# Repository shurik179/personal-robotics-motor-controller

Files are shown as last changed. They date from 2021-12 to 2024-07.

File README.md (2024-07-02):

# Personal Robotics Motor Controller

This repository contain design files for a 2-channel motor
controller board, designed by members of Personal Robotics discord server.

The controller is based on [DRV8874](https://www.ti.com/lit/ds/symlink/drv8874.pdf) motor driver ICs by TI. The  key
features of this controller are listed below:

* Support for 2 brushed DC motors, 5-24v

* Current limit per channel: 4.5A continuous (with heatsinks), current limited

* Overcurrent, undervoltage, and overtemperature protection

* Support for quadrature encoders for each motor (3.3v)

* An on-board MCU (RP2040) for reading encoder input and
  providing variety of close loop motor control modes

* Serial interface for control by a microcontroller or single board computer

This repository contains both board design files (as KiCad 6.0 project) and
firmware (written using Arduino IDE with Earl Philhower arduino-pico core for RP2040).

Detailed project information is available http://motor-controller.rtfd.io/

## Copyright

This project was started in 2021  by:

* Ichiro Furusato  (https://github.com/ifurusato)

* Adam Green (https://github.com/adamgreen/)

* shurik179 (https://github.com/shurik179)

It is released under Apache license; see file LICENSE for details.

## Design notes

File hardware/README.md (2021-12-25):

# Hardware

This directory contains:

* Board design files (in KiCad 6.0 format)

* Bill of Materials (BOM)

The board specs are:

* Dimensions: 60x50 mm

* Stackup: 4-layer, 1.6mm thickness, 1oz copper thickness (outzide layers)

* Mounting holes: 4 holes for M3 screws, in the shape of rectangle 43x53mm

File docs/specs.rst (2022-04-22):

.. _specs:
**************************
Specifications
**************************

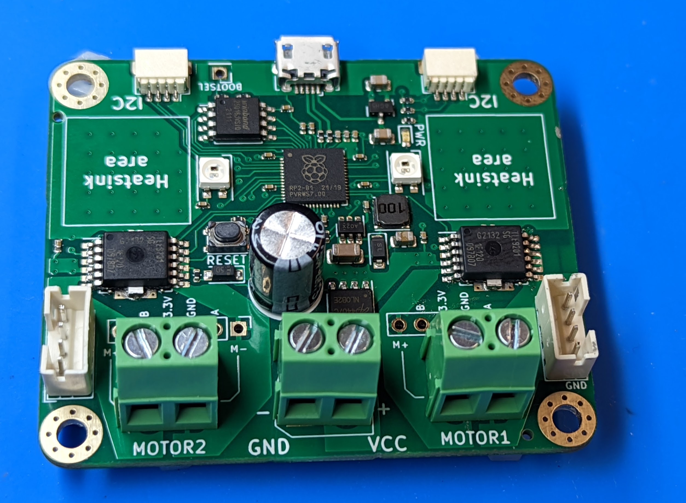
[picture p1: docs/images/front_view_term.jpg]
Top view


Overview
=========
The Personal Robotics  Motor Controller (which from now on will be abbreviated to PRMC)
can be used to control two brushed DC motors (5-18V) with quadrature encoders.
It provides position and speed reading (if encoders are present) and closed-loop
mode in which it keeps motor speed constant using encoder feedback and PID algorithm.

I2C interface
=============
PRMC is controlled by a host MCU (Arduino or similar boards) or
single board computer such as Raspberry Pi using I2C interface.
It uses 3.3v I2C bus, at up to 400 kHz speed. There are two identical
Qwiic/Stemma QT connectors allowing one to daisy-chain several controllers.

PRMC includes 10k pullups to 3.3v  on SCL and SDA lines; you might want to add
additional pullups on the i2c master.

**Important**: the 3.3v pin of the Qwiic connectors is unconnected. Instead,
PRMC uses its own voltage regulator to provide power to the built-in electronics.
This also means that when daisy-chaining, it will not provide power to other I2C devices.

By default, the controller uses I2C address `0x54` (or 84 in decimal form).
It can be changed by closing solder bridge jumpers on the bottom side  of the
board, below label `I2C ADDR`:

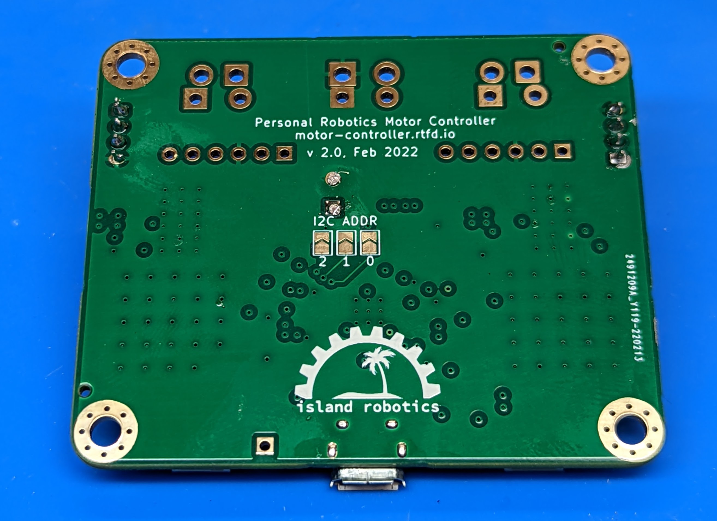
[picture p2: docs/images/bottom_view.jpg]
Bottom view


* closing jumper labeled `0` sets bit 0, adding  1 to the address

* closing jumper labeled `1` adds 2 to the address

* closing jumper labeled `2` adds 4 to the address

Thus, by using different combinations of the jumpers, one can get any address between
`0x54` (decimal 84) and `0x5A` (decimal 91), allowing one to use up to 8 such
motor controllers on the same bus.

Power supply
============
PRMC is intended for use with  motor power supply of **5--18V**. Absolute maximum
voltage for power supply is 24V; voltages above that will damage PRMC. Please
note that actual voltage provided by the battery can be higher than nominal voltage:
e.g., a 10-cell NiMH battery pack has nominal voltage of 12V but in fact a fully
charged pack can read as high as 14V.

The power supply connection has
reverse polarity protection preventing damage if the power leads are switched.
It also has limited  ESD protection to protect  it from spikes caused by electrostatic discharge.

PRMC contains a voltage regulator (a combination of buck converter and an LDO) providing
3.3v power to on-board electronics from the motor power supply.

Electronics
===========
Key components of PRMC are two `TLE9201SG <https://www.infineon.com/cms/en/product/power/motor-control-ics/brushed-dc-motor-driver-ics/integrated-full-bridge-driver/tle9201sg/>`__ motor controller
ICs by Infineon; please read the IC  datasheet for details of their operation.

PRMC also contains an RP2040 MCU by Raspberry Pi. It is preloaded with firmware
providing I2C interface, reading quadrature encoders, and providing closed loop motor control.

Indicator LEDs
==============
PRMC includes a green power indicator LED; it lights up whenever the board is powered.
In addition, it has two NeoPixel LEDs used to show the status of motors as follows:

 - Blue: firmware running, but no I2C connection yet

 - Green: motor enabled

 - Red: motor disabled (either by command from  host MCU or because of triggered
   protection such as overtemperature protection).

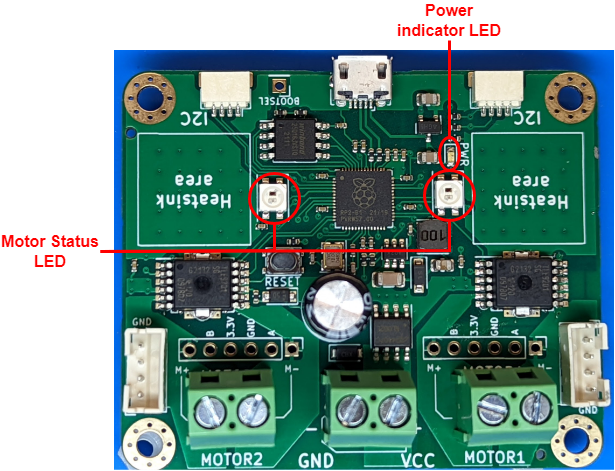
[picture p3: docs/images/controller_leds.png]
LEDs


Connections
===========

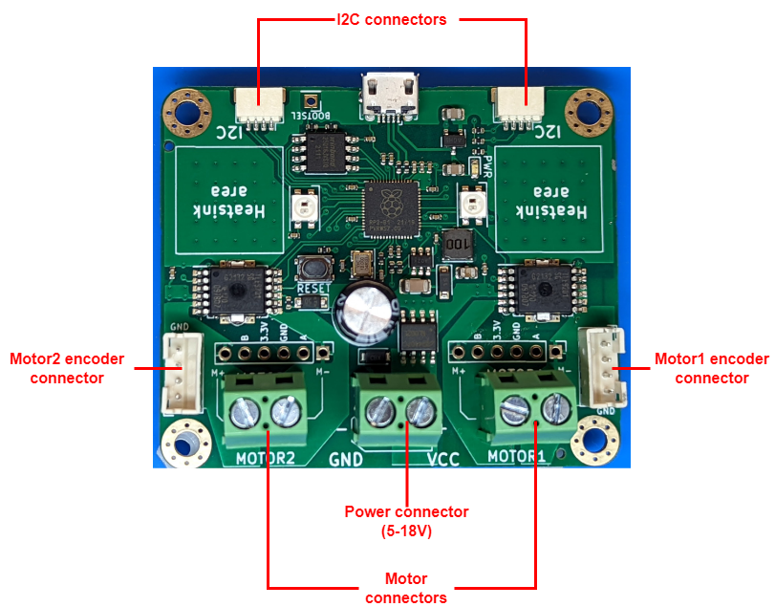
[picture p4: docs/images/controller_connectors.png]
connections


The board provides several options for connecting motors, encoders, and main power:

* Motor connections: you can choose between

  - 5mm pitch **screw terminal** (we use high-quality rising cage type terminals)

  - **JST VH** connector (same as used by First Tech Challenge robotics competitions)

  - 6pin **male headers** (matching pinout of `22mm motors <https://www.servocity.com/142-rpm-premium-planetary-gear-motor-w-encoder/>`__
    sold by Servocity). These connectors provide both motor power and encoder connectors.
    Note: 6pin  connectors used by other motors - e.g.
    `25mm motors <https://www.pololu.com/product/4865>`__ from Pololu - may use different pin order.

* Encoder connections: a 4-pin JST PH connector, using the following pin order:

  - Pin 1: GND;

  - Pin 2: 3.3V;

  - Pin 3: Channel A;

  - Pin 4: Channel B.

  (This matches the pin order of
  `REV control hub <https://www.revrobotics.com/rev-31-1595/>`__ used in First Tech Challenge robotics competitions.)

* Main power: 5mm pitch **screw terminal** or **XT30** male connector

* I2C connectors: the board provides two Qwiic/Stemma QT I2C connectors.
  This makes it possible to daisy-chain connectors. (Note: I2C connector doesn't
  provide 3.3v power, see above.)

The photos below show PRMC with different combinations of connectors.

* With  **screw terminals** for main power and motors:

   Top view

* With  **screw terminals** for main power and **male headers** for motor
  connectors

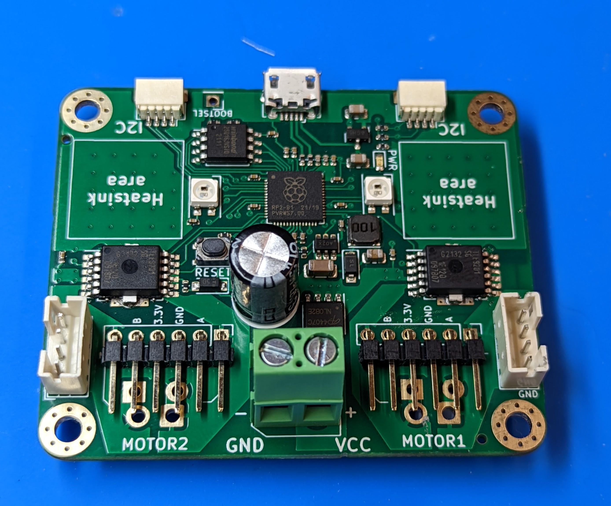
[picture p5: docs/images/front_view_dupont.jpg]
Top view
   

* With **XT30** male connector  for main power and **JST VH2** connectors for motors:

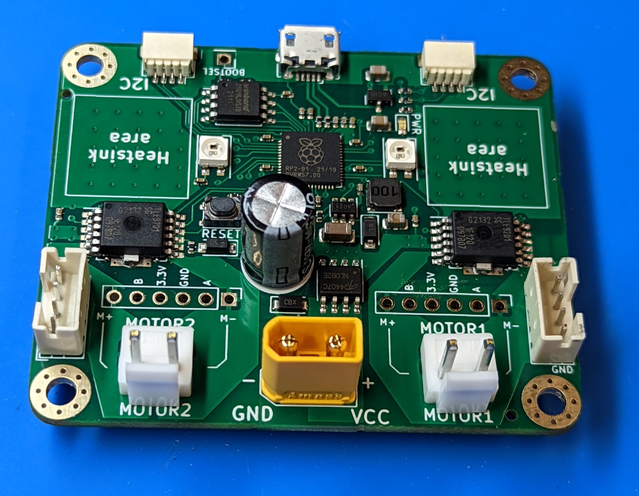
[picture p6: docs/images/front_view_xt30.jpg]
Top view
   

Current limit
=============
Motor driver ICs provide current limiting: if the output current exceeds 8A,
the drivers will start "chopping" the current, preventing it from ever exceeding 8A.
This makes it possible  to use the controller with motors with stall current over 8A.

However, 8A can only be sustained for short period of time; at this current,
the board will overheat quickly. Our testing shows that the board can continuously
provide 3.5A per channel in default configuration.

The board also contains two areas to which one can attach optional 14mm square heatsinks
(which are commonly used for Raspberry Pi single board computers and thus are
easily available from many vendors). With the heatsinks attached, the board can
provide up to 4.5A  continuous per channel.

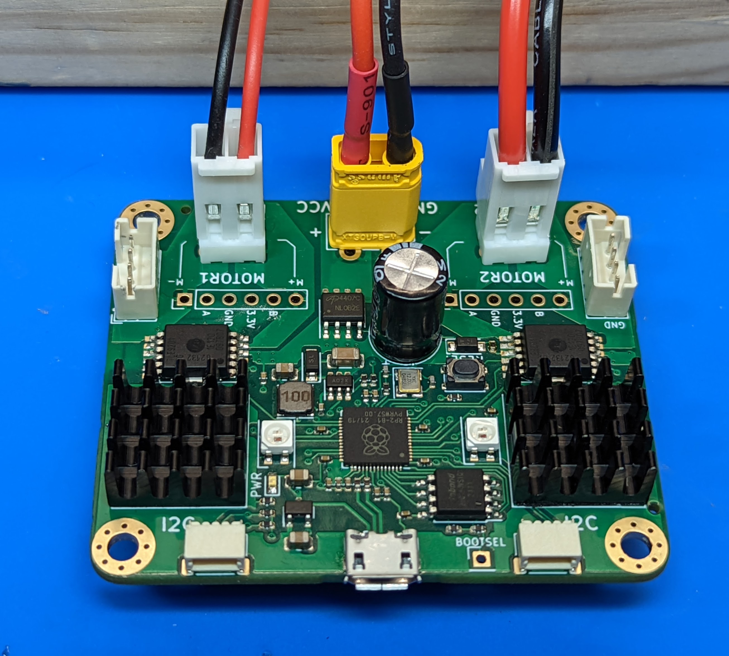
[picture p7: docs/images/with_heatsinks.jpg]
With heatsinks


Protection features
===================
In addition to current limiting listed above, the motor drivers also provide
variety of other protection features:

* undervoltage

* overtemperature

* short circuit

Please see the TLE9201 `datasheet <https://www.infineon.com/dgdl/Infineon-TLE9201SG-DS-v01_00-en.pdf?fileId=db3a304345087709014518190f481cec>`__ for details.

If any of the protection features are triggered, the IC automatically disables
motor output. Firmware allows the user to check the motor status to see if
the output has been disabled and if desired, re-enable it.

Dimensions
===========
The board dimensions are 50x60mm. Board height depends on the chosen connectors;
with screw terminals, height is about 14mm. If you use JST VH for motors or XT30
connector for power, you will need at least 22mm clearance above the PCB for the
connector and cables.

There are four mounting holes for M3 or smaller screws; their position is
shown in the diagram below.

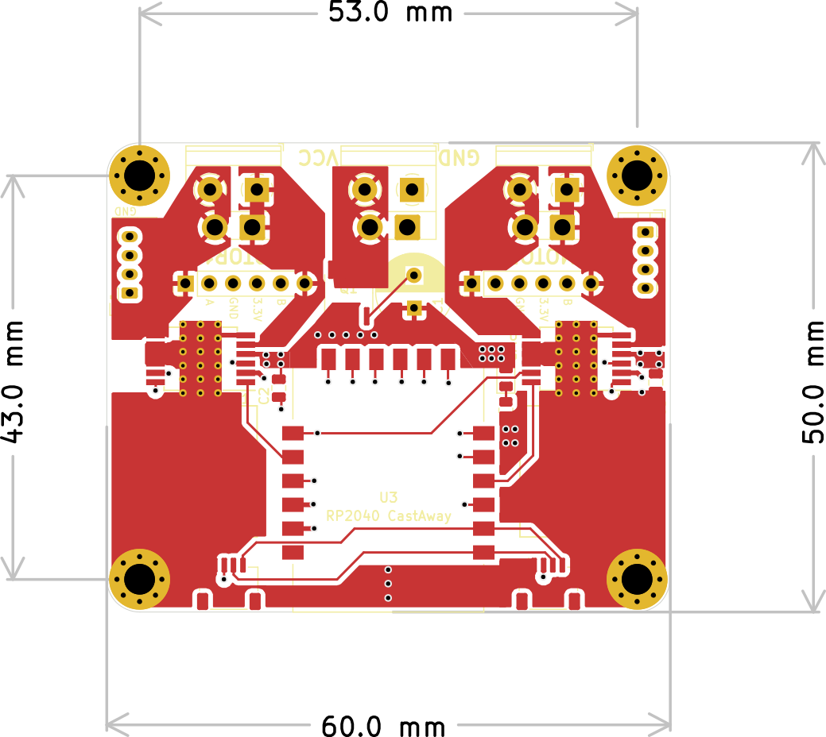
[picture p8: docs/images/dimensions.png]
Board dimensions


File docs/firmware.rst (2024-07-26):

.. _firmware:
**************************
Firmware and register map
**************************

Firmware
========

The firmware for the PRMC motor controller  is written in Arduino IDE using
Earl Philhower's `RP2040 core <https://github.com/earlephilhower/arduino-pico>`__.

If you want to modify it, you can find source files in `firmware` folder in |github|. 
Make sure to select `Boot Stage 2: W25Q16JVxQ QSPI/4` option in `Tools` menu. 

I2C communication
=================

PRMC is controlled via UART 
FIXME 
All multibyte registers use little-endian encoding; e.g. for register
`REG_POWER1`, low byte is at address 12, and high byte, at address 13.

.. csv-table:: Register map
   :widths: 10 10 30 10 50
   :header:   "register(s)","R/W","Name","data type","description"

   0,R/W,REG_ENABLE,byte,"Enable/disable motors. Bit0 controls motor1 (1=enable, 0=disable); bit1 controls motor2"
   1,R/W,REG_PID_MODE,byte,"0: normal control, PID off; 1: PID on (individual motors)"
   2-3,R/W,REG_MAX_SPEED,uint16,Max motor speed in encoder ticks/s. Required for PID
   4-5,R/W,REG_PID_KP,uint16,Kp*10^7
   6-7,R/W,REG_PID_TI,uint16,Ti*1000
   8-9,R/W,REG_PID_TD,uint16,Td*1000
   10-11,R/W,REG_PID_ILIM,uint16,Ilim
   12-13,R/W,REG_POWER1,int16,"Motor1 power, -1000...1000. Used both in PID on and PID off modes, see details in "
   14-15,R/W,REG_POWER2,int16,"Motor2 power, -1000...1000"
   16,R/W,REG_REVERSE,byte,Bit0: should readings of encoder 0 be reversed? Bit2: same for encoder2
   24,R,REG_FW_VERSION,uint8,Firmware version - minor
   25,R,,uint8,Firmware version - major
   26,R,REG_WHO_AM_I,uint8,0x54 (used for testing connection)
   27,R,REG_STATUS,uint8,"Status. Bit0 is motor1, bit1 is motor2. If motor is disabled, corresponding bit is set; otherwise, bit=0"
   28-31,R,REG_ENCODER1,int32,"Encoder 1 value, ticks"
   32-35,R,REG_ENCODER2,int32,"Encoder 2 value, ticks"
   36-37,R,REG_SPEED1,int16,"Motor 1 speed, in ticks/s"
   38-39,R,REG_SPEED2,int16,"Motor 2 speed, in ticks/s"

Motor control: basic
====================

By default, PRMC has both motor drivers enabled, with PID mode off. To set the
motor power just write a value between -1000 and 1000 to register `REG_POWER1`
for motor 1 (respectively, `REG_POWER2` for motor 2).

To disable one or both motor drivers, write the corresponding value to `REG_ENABLE`.
Note that the motor driver can also be disabled because one of the driver IC
protection features, such as overtemperature protection, were triggered.
You can check if a motor is enabled or disabled by reading `REG_STATUS`.
If necessary, you can re-enable a motor by writing to `REG_ENABLE`.

Encoders
========
PRMC supports quadrature encoders for each motor, recording encoder values
and speeds to registers `REG_ENCODERx` and `REG_SPEEDx`. It counts both
rising and falling edge for each of quadrature encoder channels, thus producing
4 ticks per encoder cycle. Both encoder values and speeds can be positive or
negative depending on the rotation direction.

Note that encoder value is recorded as 32-bit integer, so it will overflow at
2,147,483,648 ticks. Similarly, encoder speed is 16-bit integer, so it will
overflow at 32,768 ticks/s. This should be more than enough for common hobby
motors; e.g. a popular
`GoBilda Yellow Jacket <https://www.gobilda.com/5202-series-yellow-jacket-planetary-gear-motor-26-9-1-ratio-223-rpm-3-3-5v-encoder/>`__
motor has  no-load  speed of about 3000 encoder ticks/s.

For normal operation of PID control (see next section), it is expected that
providing positive power to the motor gives positive speed as measured by the encoder.
If your motor and encoder are wired so that positive power to motor gives negative
encoder counts, you can either change the wiring, or change the encoder direction
in software by writing to `REG_REVERSE`.

PID control
===========

Motor driver firmware provides an option of closed loop motor control. In this mode,
the controller tries to keep the speed of each motor (as measured using encoders)
as close as possible to the desired speed, using industry-standard PID
(proportional-integral-derivative) algorithm.

The motor power is determined by the standard formula of PID algorithm:

.. math::
   M=M_0+ P + I_{clipped} + D

where:

:math:`M` is motor power (ranging from -1.0 to 1.0)

:math:`M_0=v_{target}/v_{max}` is the zero-level approximation; here
:math:`v_{target}` is the requested speed (in ticks/s) and :math:`v_{max}` is the maximal
possible motor speed, which is determined by motor's no-load RPM

:math:`P=K_p e` is the proportional term. Here
:math:`e=v_{target}-v_{actual}` is the error, i.e. the  difference of desired and actual motor
speeds (measured in encoder ticks/sec) and :math:`K_p` is a coefficient

:math:`I=\frac{K_p}{T_i}\int e dt` is the integral term; :math:`I_{clipped}` is
:math:`I` but clipped to be between :math:`-I_{lim}` and :math:`I_{lim}`

:math:`D=K_p T_d \frac{d}{dt} e` is the  derivative
of the error

:math:`K_p, T_i, T_d, I_{lim}` are the PID coefficients. They **must  be set
(by writing to corresponding registers) before PID mode can be used**; there
are no default values.

The behavior of the PID algorithm is determined by these coefficients; for
example, if the coefficient :math:`K_p` is too small, it will take the motor a
long time to stabilize to the desired speed; if the coefficient :math:`K_p` is
too large, you might get oscillations. Choosing the correct coefficients
requires significant experience and is certainly outside the scope of this user
guide.

Please note that current version of firmware uses same PID coefficients for
both motors; setting them independently for the two motors is not supported.

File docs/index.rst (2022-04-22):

##################################
Personal Robotics Motor Controller
##################################
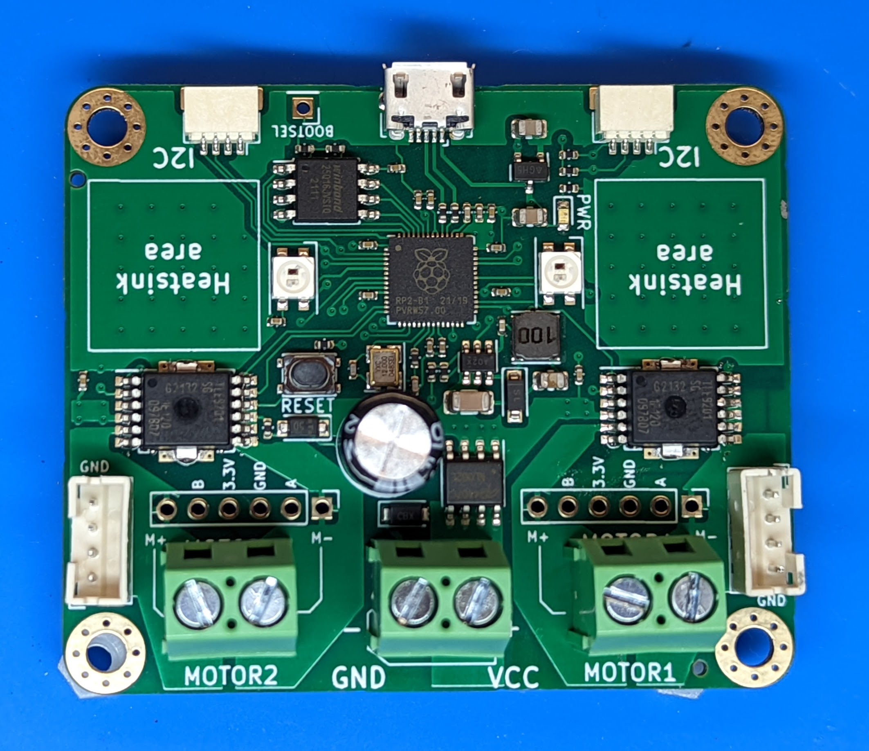
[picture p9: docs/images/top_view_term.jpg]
Motor driver


This guide contains documentation for a dual channel controller for DC motors.
This controller was created by group of robotics enthusiasts from Personal Robotics
discord server, who needed a mid-power dual channel motor controller supporting
closed loop motor control but were not ready to pay $70 and more for existing
commercial realizations. So we created our own - and made it available on Tindie:
https://www.tindie.com/products/26573/

Key features of this controller are as follows:

* support for **2 brushed DC motors**

* Motor voltage: **5-18v**; reverse polarity protection for power input

* Current per channel

  - **8A peak**, current limited

  - **3.5A continuous** if used without heatsinks

  - **4.5A continuous** with optional heatsinks

* Support for **quadrature encoders**  for each channel. Note: it uses
  **3.3v for encoders** - make sure your encoders support that (many encoders
  require 3.5V or above)

* **Closed loop speed control**, using PID algorithm

* Variety of **protection features**: automatic overcurrent, overtemperature,
  undervoltage, and short circuit protection

* Controlled by a host microcontroller  or single board computer such as Raspberry Pi
  using **I2C interface**. MicroPython library is available

All design files and software are available from the project |github| under open
source license.

This document describes version 2.0 of the project, released in April 2022.

.. toctree::
    :caption: Table of Contents
    :maxdepth: 1

    specs
    firmware
    mp_library
    license

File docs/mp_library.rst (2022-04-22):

.. _library:
**************************
Micropython Library
**************************
This chapter documents included Micropython library.

Installation
============
To install the library, download the latest version of `PRMC.py` file
from `mp_library` folder in |github| and copy it to the root directory of your board.

Basic example
=============

Below is the basic example of Micropython code using the library.

.. code-block:: python

    from machine import Pin, I2C
    from time import sleep
    import PRMC
    i2c = I2C(0, scl=Pin(9), sda=Pin(8), freq=100000)

    driver = PRMC.controller(i2c)

    print("Motor controller initialized.")
    print("Firmware version: " + driver.fw_version()))
    # driver.reverse_encoder(0)
    driver.set_motors(0.5) #set speed of both motors to 50%
    while True:
        driver.get_encoders()
        driver.get_speeds()
        print("Encoders: {} {}. Speeds: {} {}".format(driver.encoder[0],driver.encoder[1], driver.speed[0], driver.speed[1] ))
        sleep(0.5)

Full documentation
==================

In all the functions which use `motor` as an argument, value of 0 corresponds to
Motor1, and value of 1, to Motor2.

Initialization and basic info
-----------------------------

.. function:: controller(i2c, address=0x54)

    Creates and initializes motor controller object. If connection can't be established
    (e.g. because the driver is not connected or malfunctions), a `RuntimeError` 
    exception will be raised.
    Optional parameter `address` is the I2C address. If omitted, default value of
    `PRMC_DEFAULT_I2C_ADDRESS=0x54` is used.

.. function:: fw_version()

   Returns firmware version as a string, in format `major.minor`, e.g. `1.99`

.. function:: disable(motor_combo)

   Disable motor outputs. Possible values for `motor_combo` are:

   * `1`: disable motor 1, enable motor 2

   * `2`: enable motor 1, disable motor 2

   * `3`: disable both motors

.. function:: enable(motor_combo)

   Opposite of the previous command, setting which motors should be enabled.

   Possible values for `motor_combo` are:

  * `1`: enable motor 1, disable motor 2

  * `2`: disable motor 1, enable motor 2

  * `3`: enable both motors

  Note: according to the datasheet, if a motor driver was disabled by a triggered
  protection feature (e.g., overtemperature protection), to enable it again you need
  to first send disable signal and then enable signal:

  .. code-block:: python

      driver.disable(1) # to disable motor 1, leaving motor 2 enabled
      driver.enable(3)  # to reenable both motors

.. function:: motor_status(motor)

    Returns the motor status.
    If motor is enabled, status is 0; if it is disabled, status is 1.
    Note that motor can be disabled either because the user disabled it using `disable`
    function above, or because one of the protection features (overcurrent,
    overtemperature, short circuit) was triggered.

    Overtemperature and other protection features are latching: if the
    protection was triggered, the motor stays disabled even after the
    temperature/voltage returns to normal. To re-enable the motors, use `enable` command above.

Basic motor control
-------------------

.. function:: set_motor(motor, power)

   Sets the power for given motor.
   The power ranges between -1.0 (full speed backwards) to 1.0 (full speed forwards)

.. function:: set_motors(power1, power2 = None)

   Set power for both motors in one command. Argument `power2` is optional;
   if omitted, same power is given to both motors.

Encoders and speed
------------------

.. function:: get_encoder(motor)

   Returns current encoder reading (ticks) for given motor. If encoder is absent or
   disconnected, returns 0.

   When counting ticks, both rising and falling edge is counted, for each of 2 channels.
   Thus, we get 4 ticks per period.

.. function:: get_speed(motor)

   Returns current speed reading for given motor, in ticks/sec.

.. function:: get_encoders()

   Gets from the controller and saves readings of both encoders. These readings
   can be accessed using properties `controller.encoder[0]` and `controller.encoder[1]`.

   Using this method instead of `get_encoder(0)` followed by `get_encoder(1)` ensures
   that both encoder readings were taken at same moment of time, which might be
   important when comparing them.

.. function:: get_speeds()

    Gets from the controller and saves readings of both speeds. These readings
    can be accessed using properties `controller.speed[0]` and `controller.speed[1]`.
    As before, advantage of this method is that both speeds are read at the same moment of time.

.. function:: reverse_encoder(motor)

   After calling this function, all future readings of this encoder will be
   reversed (multiplied by -1). This is convenient if your encoder and motor are wired so that
   positive power to the motors caused speed measured by encoder to be negative.

PID configuration
-----------------
To use PID mode (as described in `Firmware` section), you need to set PID
coefficients. You can do it using functions below.

.. function:: configure_pid(maxspeed, Kp, Ti, Td, Ilim)

   Sets the PID coefficients for both motors. Note that these coefficients are
   only used if you enable PID using `pid_on()` command below.

.. function:: configure_pid(maxspeed)

   Sets default PID coefficients, based on motor maximal speed (in ticks/s).
   The default values are as follows:

.. code-block:: python

    Kp = 0.8/maxspeed
    Ti = 0.3
    Td = 0.03
    Ilim = 1000

These values are somewhat conservative: while they are unlikely to cause
oscillations, it may take some time for the motor speed to stabilize. You may
experiment with these values to improve performance of the PID loop.

.. function:: pid_on()

   Enables PID for both motors. This assumes that PID has been configured
   previously using `configure_pid()` command.

   After enabling PID, any power given to the motors using  `set_motor` commands
   will be actively maintained using PID algorithm.

.. function:: pid_off()

   Disables PID for both motors.

It is suggested that you only use the commands above when the motors are stopped.
Changing PID settings while the motors are in motion can lead to unexpected results.

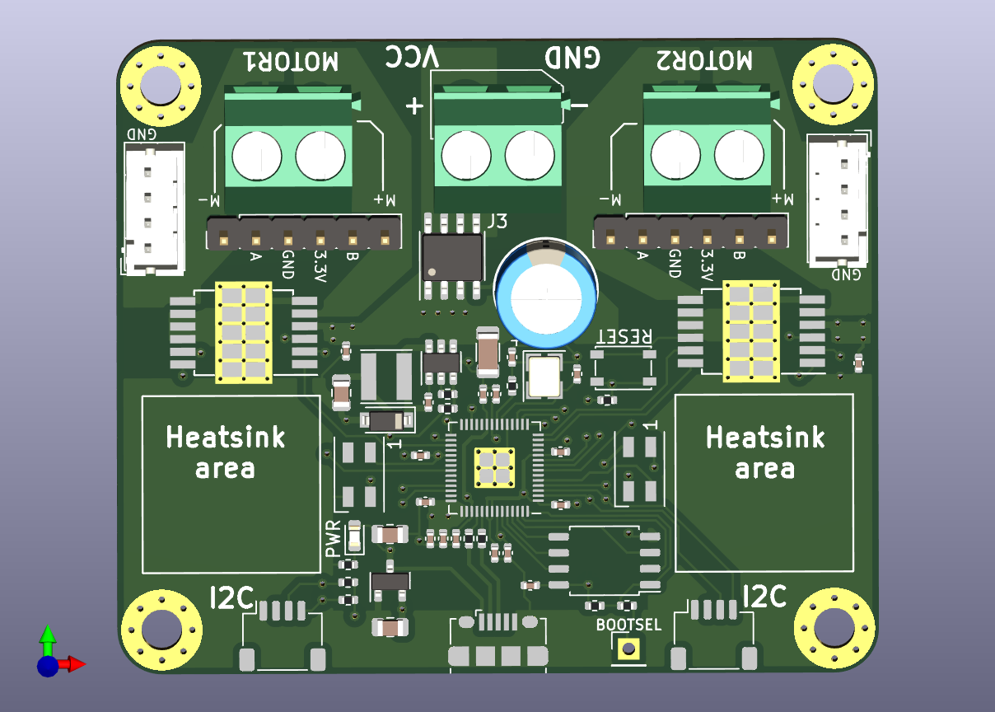
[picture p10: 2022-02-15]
hardware/motor-driver.png

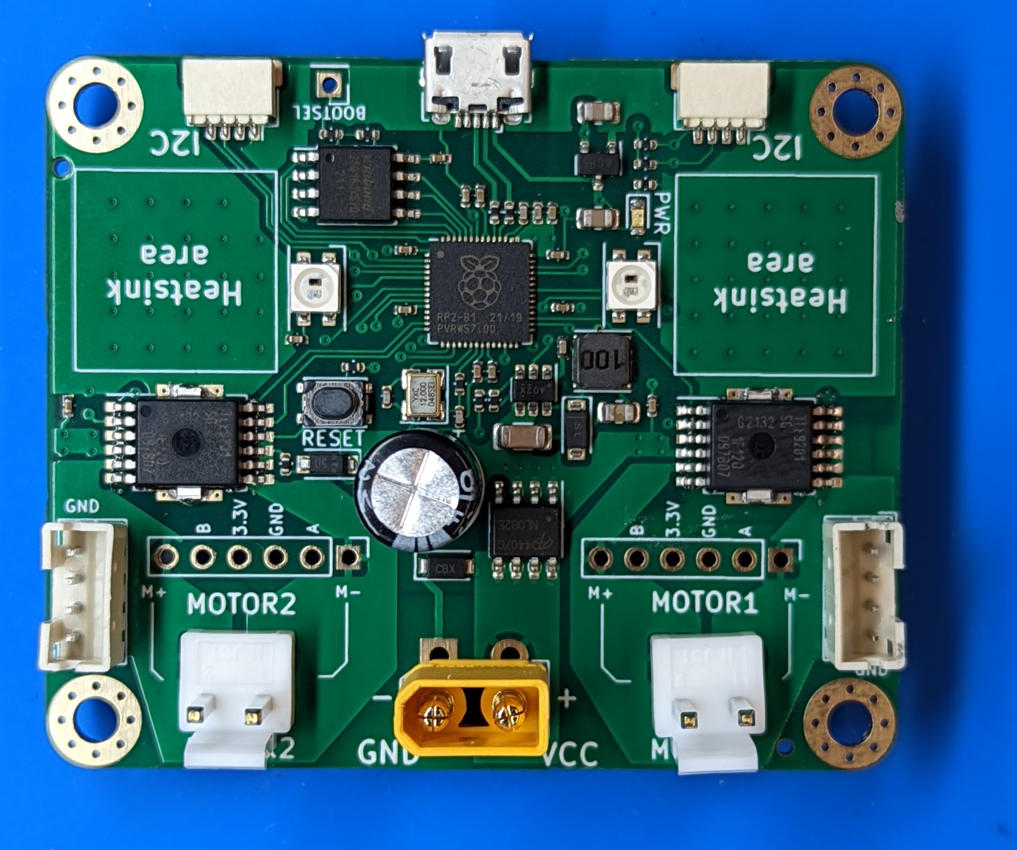
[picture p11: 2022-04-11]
docs/images/top_view_xt30.jpg

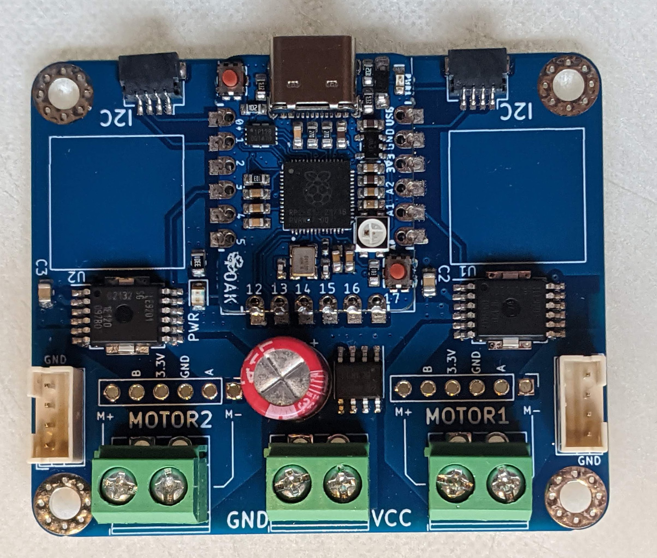
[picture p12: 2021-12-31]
docs/images/top_view.jpg

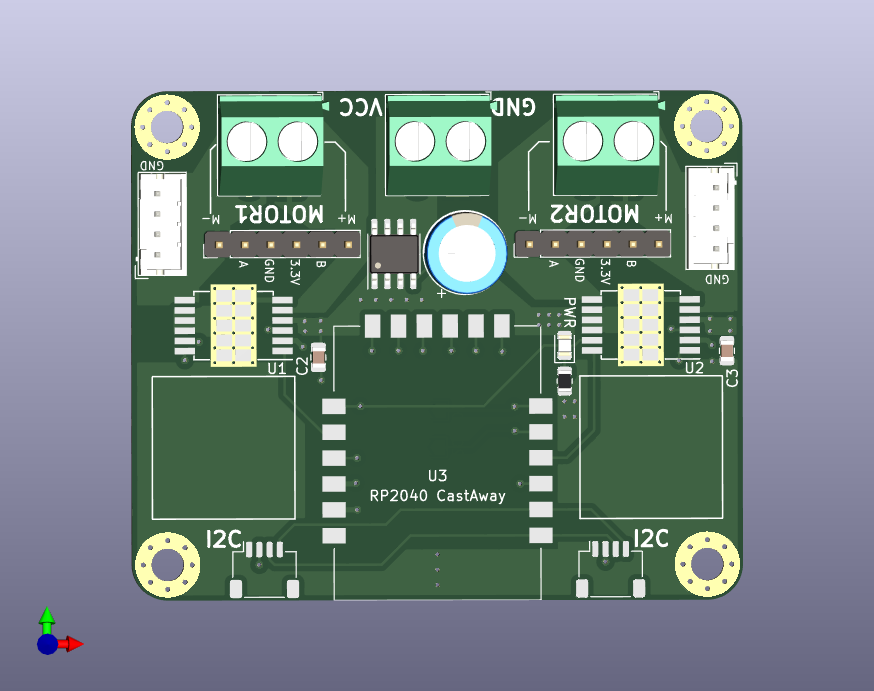
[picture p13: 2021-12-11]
motor-driver.png

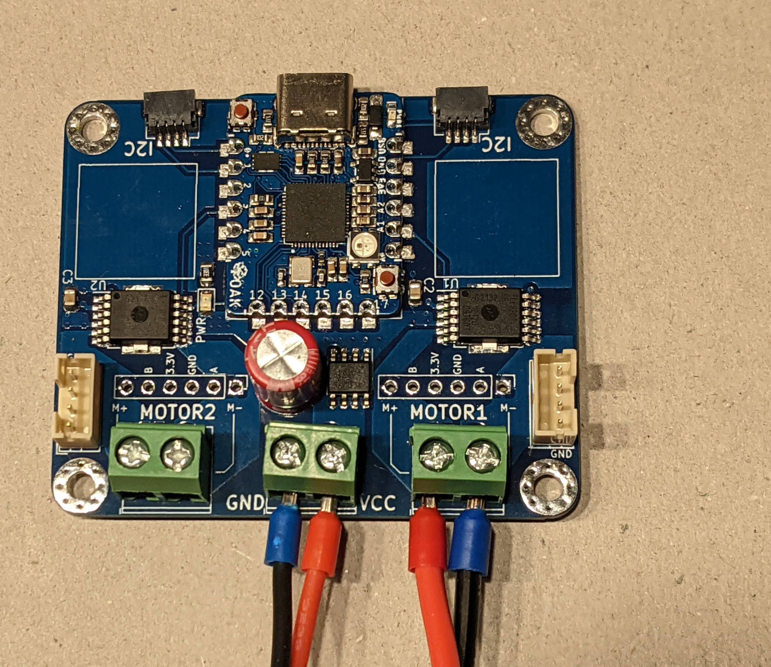
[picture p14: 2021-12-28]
docs/images/main_photo.jpg

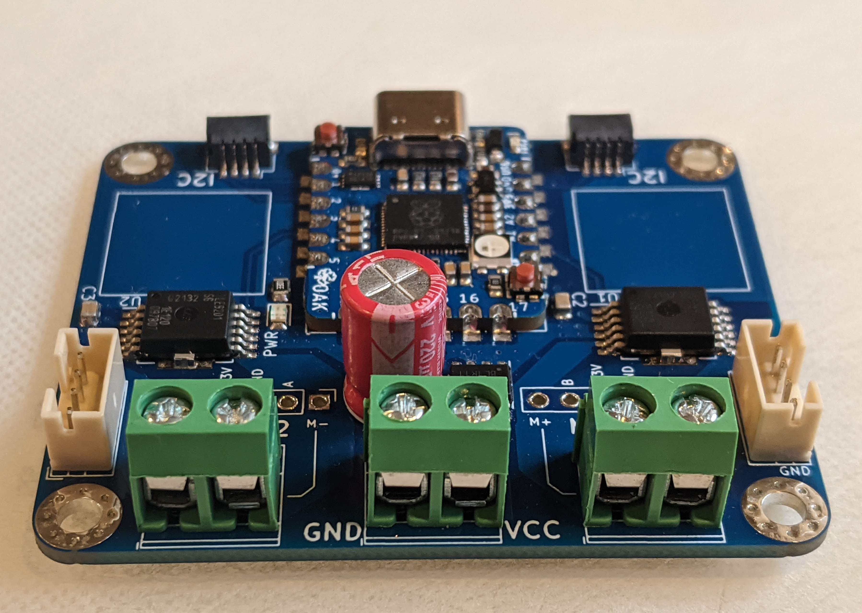
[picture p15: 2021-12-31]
docs/images/front_view.jpg

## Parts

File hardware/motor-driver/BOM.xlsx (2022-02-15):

Component | Description | Part Number | References | Value | Footprint | Quantity Per PCB | Datasheet | LCSC | Comment
1 | AL electrolytic capacitor,220uF |  | C1, | 220uF | Radial_D8.0mm_P3.50mm | 1
2 | SMD capacitor, 10 uF, 16V |  | C2, C3, C22 | 10uF | 0805 | 3 |  | C15850
3 | SMD capacitor, 10 uF, 50V |  | C4, | 10uF | 1206 | 1 |  | C13585
4 | SMD capacitor |  | C5, C6, | 1uF | 0402 | 2 |  | C52923
5 | SMD capacitor |  | C7, C8, C9, C10, C11, C12, C13, C14, C15, C16, C17, C18, C23 | 100nF | 0402 | 13 |  | C1525
6 | SMD capacitor |  | C19 | 220nF | 0402 | 1 |  | C16772
7 | SMD capacitor |  | C20, C21, | 30pF | 0402 | 2 |  | C1570
8 | LED, green |  | D1, | LED | 0603 | 1 |  | C72043
9 | Schottky diode | B5819W | D2, |  | SOD123 | 1 |  | C8598
10 | RGB LED with integrated controller | WS2812B-mini | D3, D4, |  | 3535 | 2 |  | C527089
11 | JST SH 4p connector, horizontal | A1002WR-S-4P | J6, J7 |  |  | 2 |  | C239522
12 | USB Micro Type B connector | 10118194-0001LF | J14, |  |  | 1 |  | C132563
13 | Inductor, 10uH, 1A | SWPA4012S100 | L1, | 10uH | Inductor 4.0x4.0mm | 1 |  | C36405
14 | P-Channel Power MOSFET, SO-8 | AO4407C | Q1, | AO4407C | SOIC8 | 1 |  | C469397
15 | SMD resistor, 3.3k, 0402 |  | R1, | 3.3k | 0402 | 1 |  | C25890
16 | SMD resistor, 1k, 0402 |  | R2, R4, | 1k | 0402 | 2 |  | C11702
17 | SMD resistor, 10k, 0402 |  | R3, R7,R8,R9,R10 | 10k | 0402 | 5 |  | C25744
18 | SMD resistor, 27R, 0402 |  | R5, R6, | 27R | 0402 | 2 |  | C25100
19 | SMD resistor, 54.9k, 0402 |  | R11, | 54.9k | 0402 | 1 |  | C11626
20 | Push button switch, generic, two pins | PTS810SJM250 | SW1, | PTS810SJM250 | 3.2x4.2mm | 1 |  | C116501
21 | Brushed DC Motor Driver, PWM Control, 45V, 3.6A, Current limiting, HTSOP-8 | TLE9201SG | U1, U2, | TLE9201SG | SO-12 | 2 |  | C2653438
22 | 600mA 42V Input Step-Down DC-DC Regulator, Adjustable Output Voltage, 550kHz, TSOT-23-5 | LV2842XLVDDCR | U3, | LM2842X | SOT-23-6 | 1 |  | C225807
23 | 300mA low dropout linear regulator, shutdown pin, 2.5V-6V input voltage, 3.3V fixed positive output, SOT-23 package | AP2120N-3.3 | U4, | AP2120N-3.3 | SOT-23-3 | 1 |  | C155508
24 | RP2040 32bit MCU | RP2040 | U5, | RP2040 | QFN-56 | 1 |  | C2040
25 | 16Mb Serial Flash Memory, Standard/Dual/Quad SPI, SOIC-8 | W25Q16JVSSIQ | U6, | W25Q16JVSSIQ | SOIC8-208mil | 1 |  | C82317
26 | Four pin crystal, GND on pins 2 and 4 | Crystal_GND24 | Y1, | X322512MSB4SI | 3.2x2.5mm | 1 |  | C9002

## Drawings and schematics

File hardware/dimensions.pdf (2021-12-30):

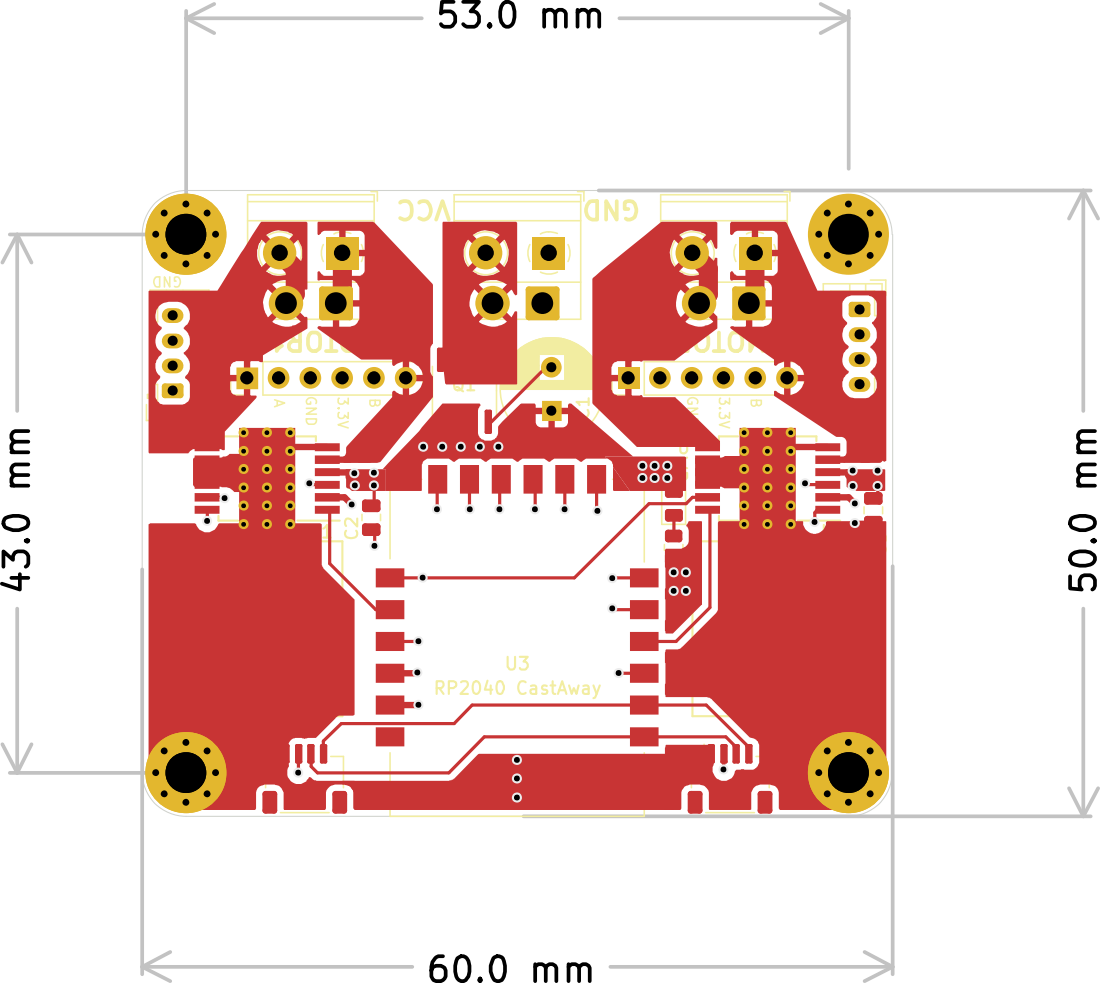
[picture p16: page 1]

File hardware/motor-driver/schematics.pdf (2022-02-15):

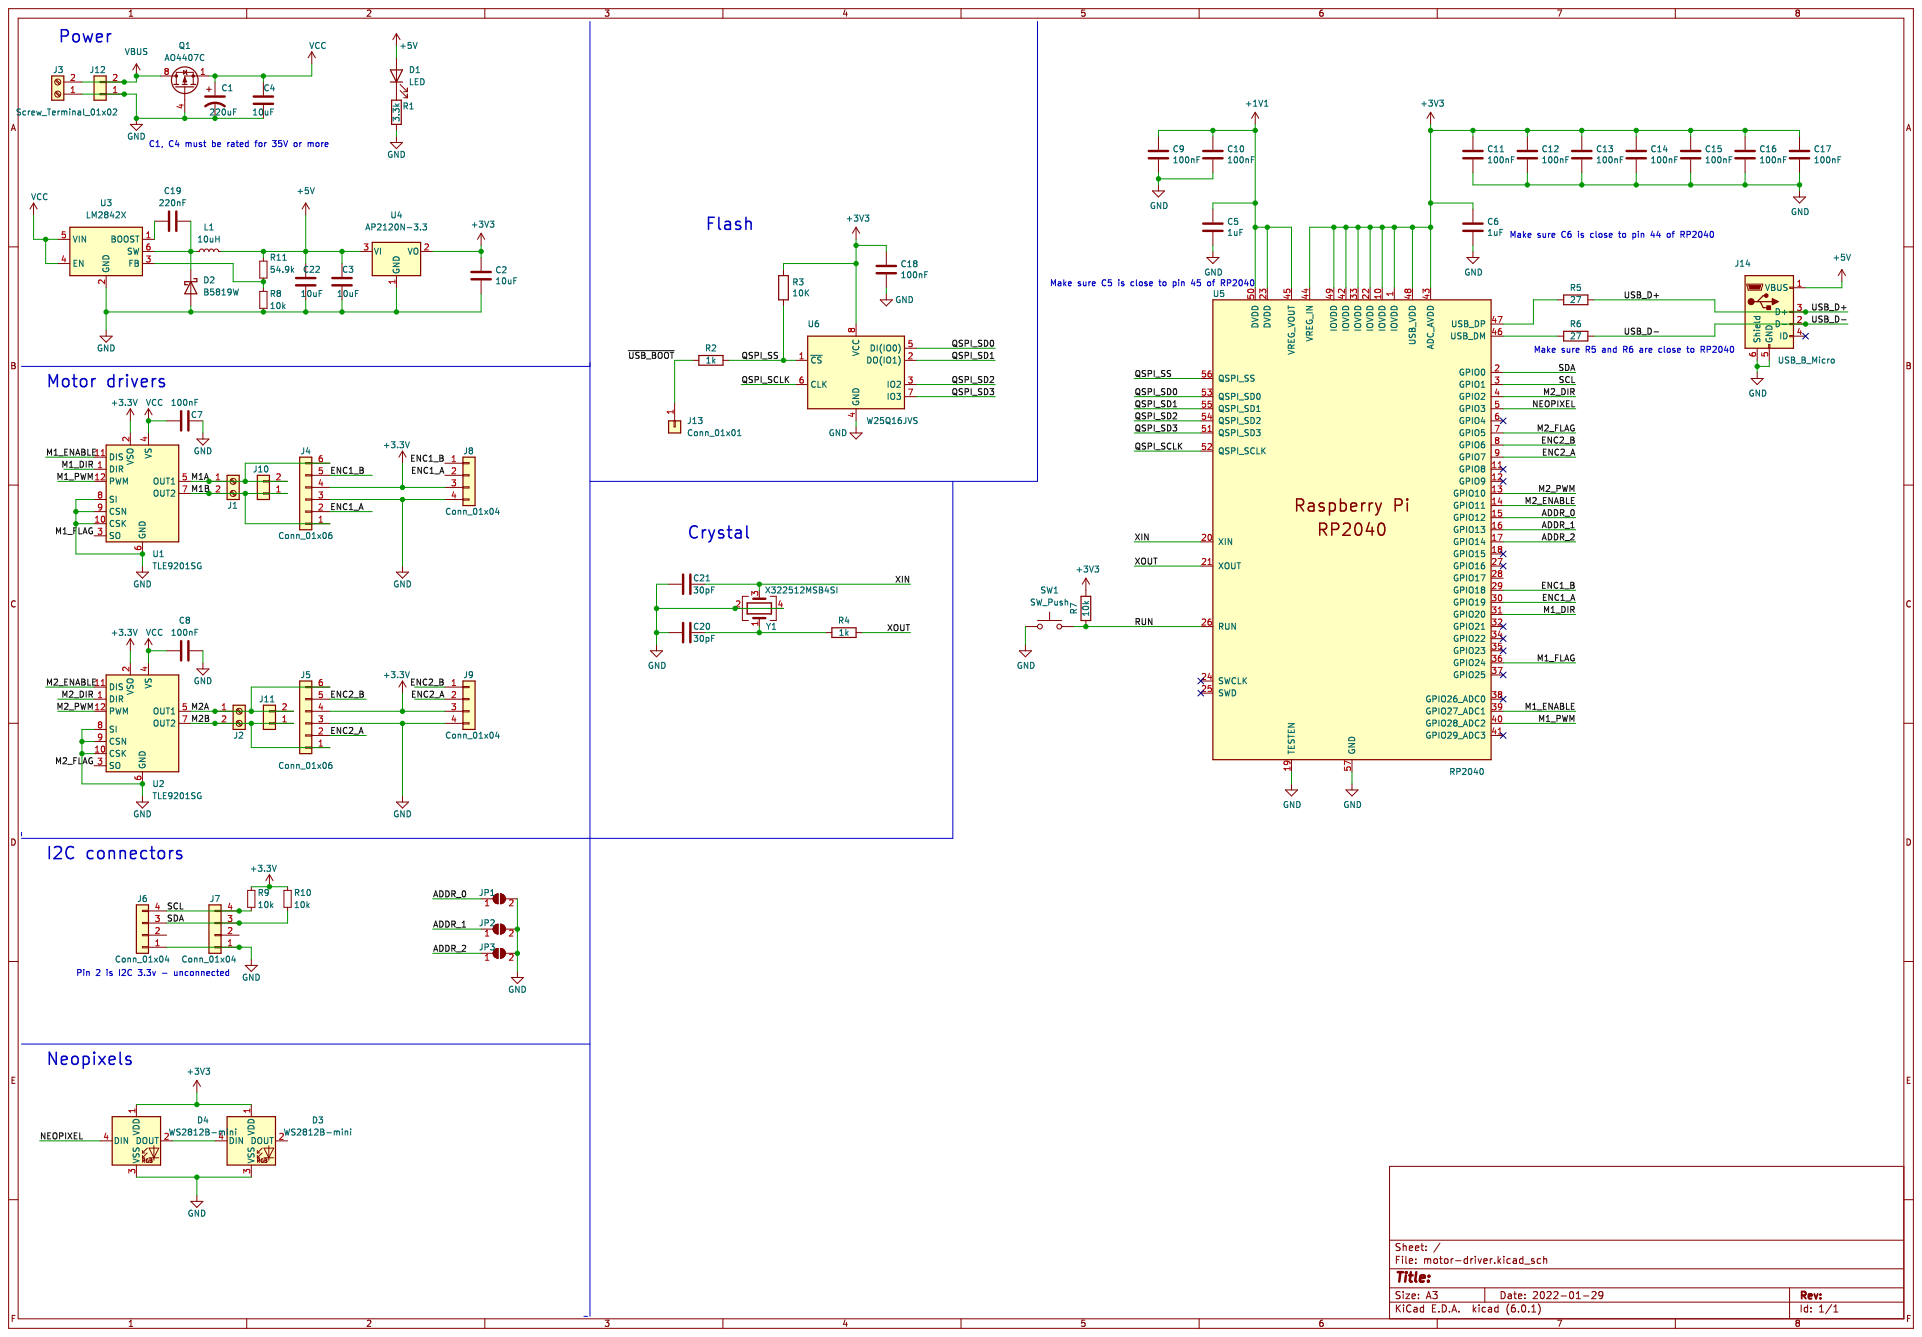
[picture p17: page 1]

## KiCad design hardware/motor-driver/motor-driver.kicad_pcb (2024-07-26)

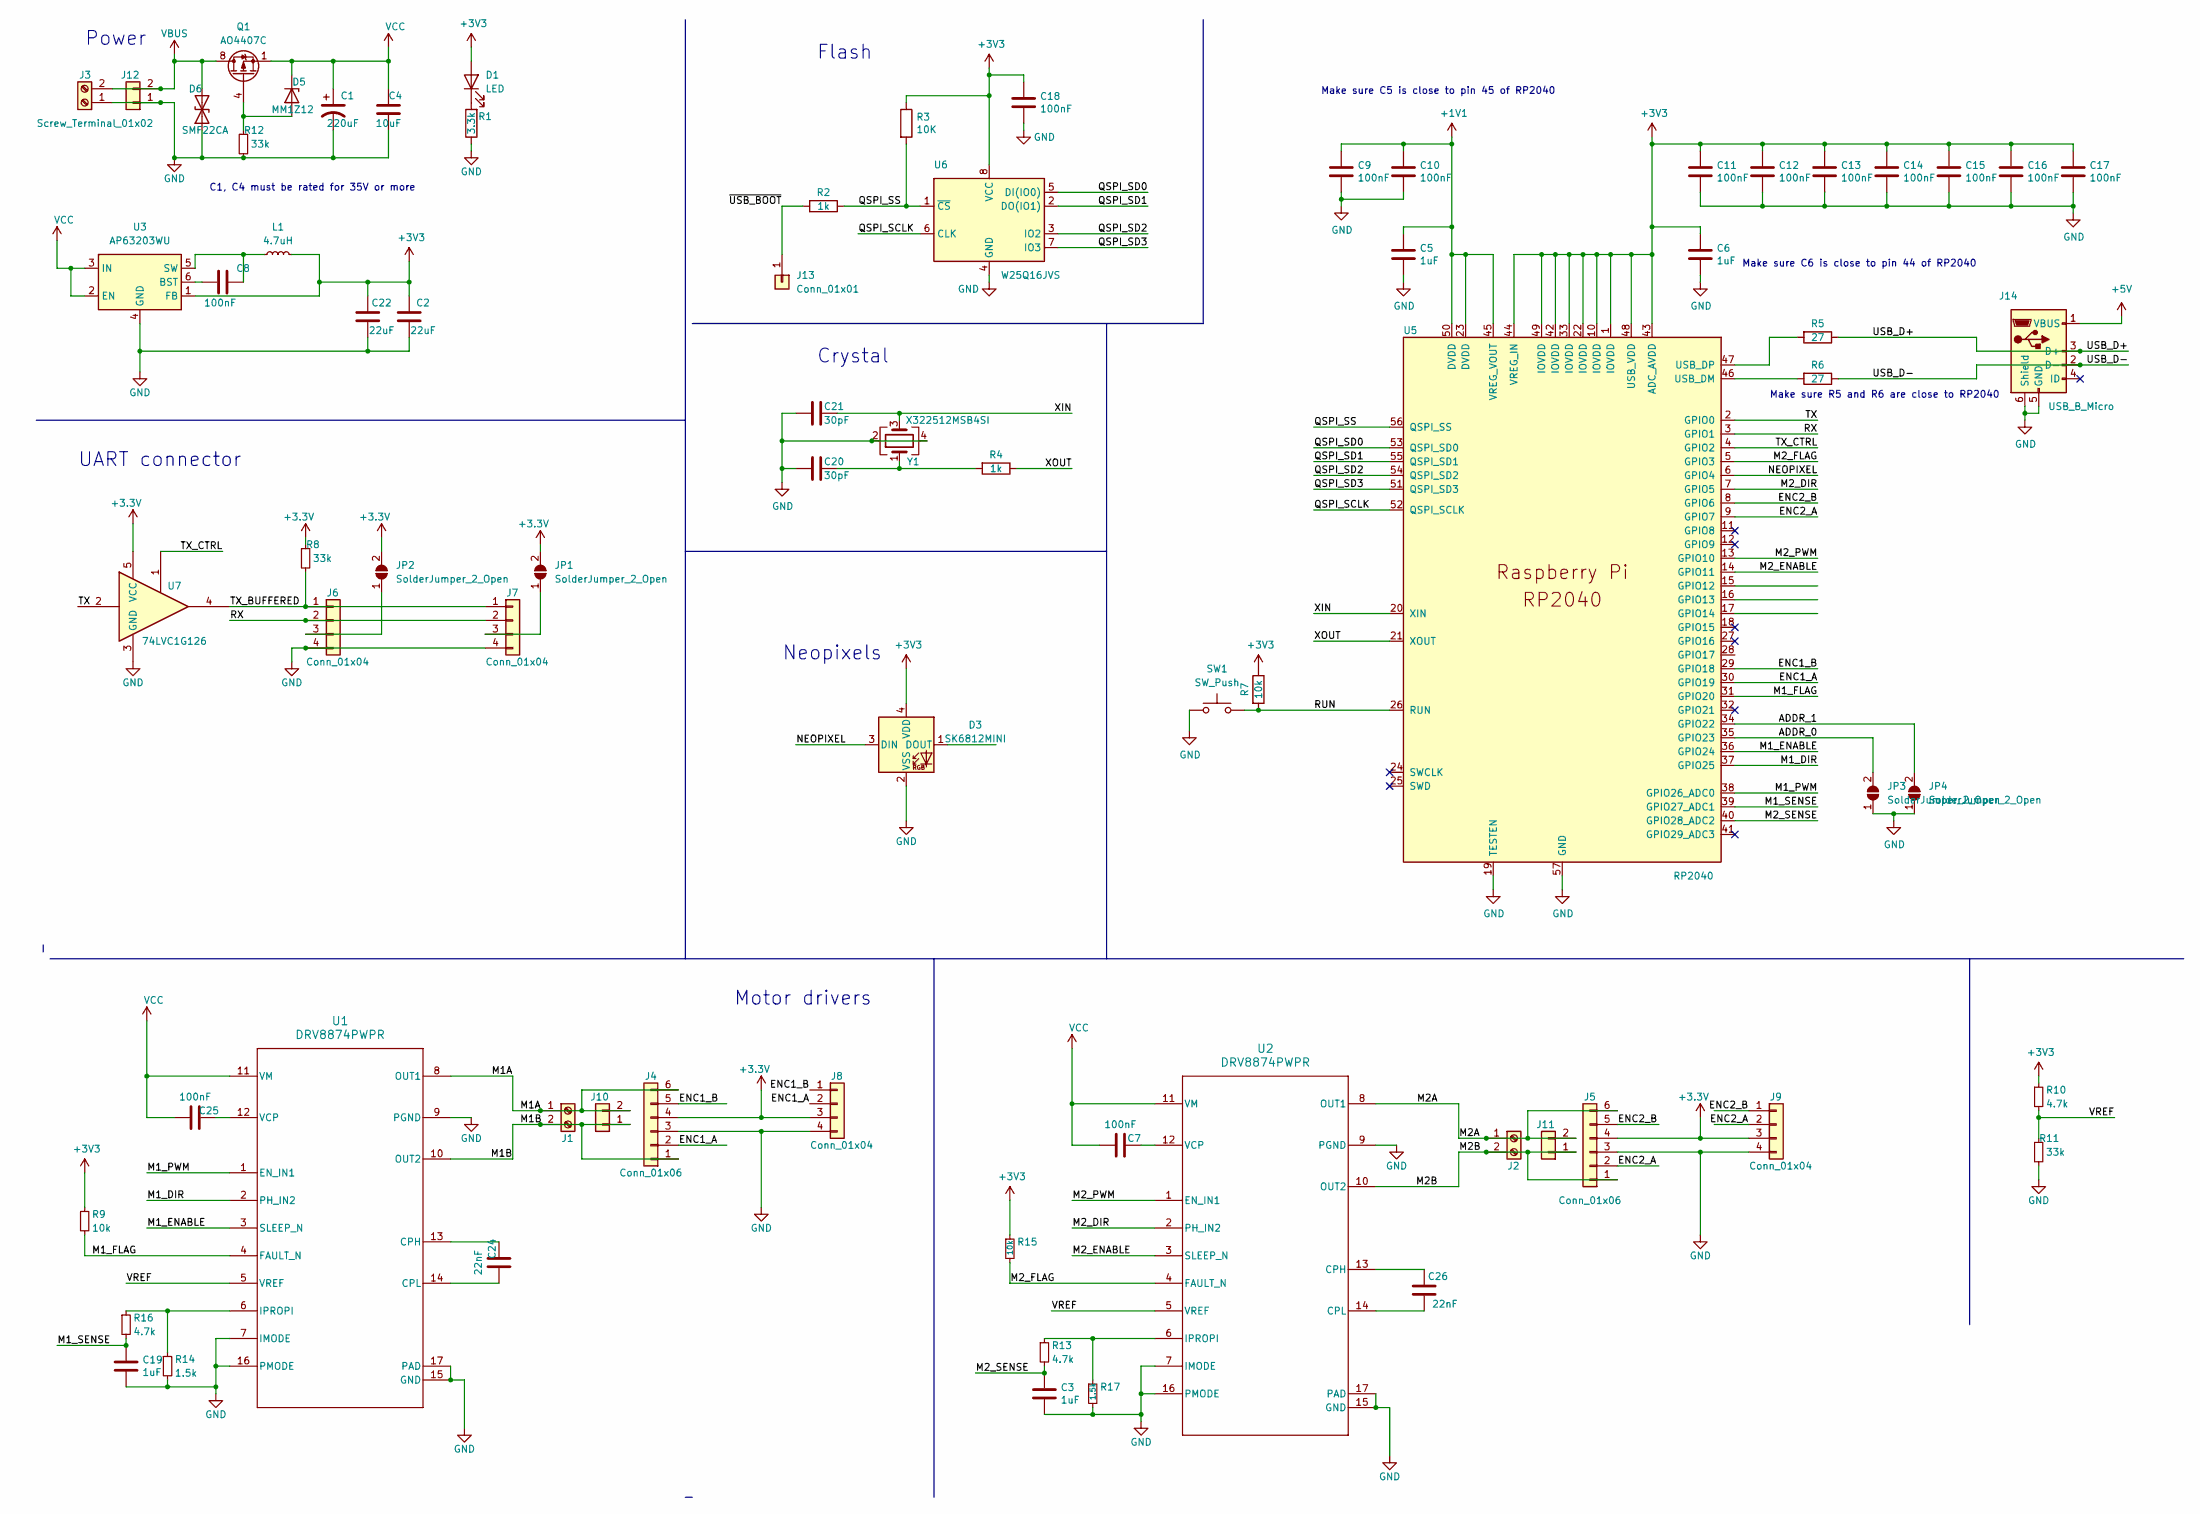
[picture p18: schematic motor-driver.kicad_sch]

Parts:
C1: 220uF; CP_Radial_D8.0mm_P3.50mm
C2, C22: 22uF; C_0805_2012Metric; LCSC C45783
C3, C5, C6, C19: 1uF; C_0402_1005Metric; LCSC C52923
C4: 10uF; C_1206_3216Metric; LCSC C13585
C7, C8, C9, C10, C11, C12, C13, C14, C15, C16, C17, C18, C25: 100nF; C_0402_1005Metric; LCSC C1525
C20, C21: 30pF; C_0402_1005Metric; LCSC C1570
C24, C26: 22nF; C_0402_1005Metric; LCSC C1532
D1: LED; LED_0805_2012Metric; LCSC C2297
D3: SK6812MINI; LED_SK6812MINI_PLCC4_3.5x3.5mm_P1.75mm; LCSC C2886570
D5: MM1Z12; D_SOD-123; LCSC C86234
D6: SMF22CA; D_SOD-123F; LCSC C353295
J1, J2, J3: Screw_Terminal_01x02; TerminalBlock_Phoenix_MKDS-1,5-2_1x02_P5.00mm_Horizontal_no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
J4, J5: Conn_01x06; PinHeader_1x06_P2.54mm_Vertical
J6, J7, J8, J9: Conn_01x04; JST_PH_B4B-PH-K_1x04_P2.00mm_Vertical
J10, J11: Conn_01x02; JST_VH_B2P-VH-B_1x02_P3.96mm_Vertical-nosilk
J12: Conn_01x02; AMASS_XT30UPB-M_1x02_P5.0mm_Vertical
J13: Conn_01x01; PinHeader_1x01_P2.54mm_Vertical
J14: USB_B_Micro; USB_Micro-B_Amphenol_10118194_Horizontal; LCSC C132563
JP1, JP2, JP3, JP4: SolderJumper_2_Open; SolderJumper-2_P1.3mm_Open_TrianglePad1.0x1.5mm
L1: 4.7uH; L_Sunlord_SWPA4018S; LCSC C60117
Q1: AO4407C; SOIC-8_3.9x4.9mm_P1.27mm; LCSC C469397
R1: 3.3k; R_0402_1005Metric; LCSC C25890
R2, R4: 1k; R_0402_1005Metric; LCSC C11702
R3: 10K; R_0402_1005Metric; LCSC C25744
R5, R6: 27; R_0402_1005Metric; LCSC C25100
R7, R9, R15: 10k; R_0402_1005Metric; LCSC C25744
R8, R11, R12: 33k; R_0402_1005Metric; LCSC C25779
R10, R13, R16: 4.7k; R_0402_1005Metric; LCSC C25900
R14, R17: 1.5k; R_0402_1005Metric; LCSC C25867
SW1: SW_Push; SW_SPST_PTS810; LCSC C116501
U1, U2: DRV8874PWPR; HTSSOP-16-1EP_4.4x5mm_P0.65mm_EP3.4x5mm_Mask2.46x3.55mm_The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; LCSC C1855818
U3: AP63203WU; TSOT-23-6; LCSC C780769
U5: RP2040; RP2040-QFN-56; LCSC C2040
U6: W25Q16JVS; SOIC-8_5.23x5.23mm_P1.27mm; LCSC C82317
U7: 74LVC1G126; SOT-23-5; LCSC C7834
Y1: X322512MSB4SI; Crystal_SMD_Abracon_ABM8G-4Pin_3.2x2.5mm; LCSC C9002

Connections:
+1V1: C5.1, C9.1, C10.1, U5.23 (DVDD), U5.45 (VREG_VOUT), U5.50 (DVDD)
+5V: J14.1 (VBUS)
/ADDR_0: JP3.2 (B), U5.35 (GPIO23)
/ADDR_1: JP4.2 (B), U5.34 (GPIO22)
/ENC1_A: J4.2, J8.2, U5.30 (GPIO19)
/ENC1_B: J4.5, J8.1, U5.29 (GPIO18)
/ENC2_A: J5.2, J9.2, U5.9 (GPIO7)
/ENC2_B: J5.5, J9.1, U5.8 (GPIO6)
/M1A: J1.1, J4.6, J10.2, U1.8 (OUT1)
/M1B: J1.2, J4.1, J10.1, U1.10 (OUT2)
/M1_DIR: U1.2 (PH_IN2), U5.37 (GPIO25)
/M1_ENABLE: U1.3 (SLEEP_N), U5.36 (GPIO24)
/M1_FLAG: R9.2, U1.4 (FAULT_N), U5.31 (GPIO20)
/M1_PWM: U1.1 (EN_IN1), U5.38 (GPIO26_ADC0)
/M1_SENSE: C19.1, R16.2, U5.39 (GPIO27_ADC1)
/M2A: J2.1, J5.6, J11.2, U2.8 (OUT1)
/M2B: J2.2, J5.1, J11.1, U2.10 (OUT2)
/M2_DIR: U2.2 (PH_IN2), U5.7 (GPIO5)
/M2_ENABLE: U2.3 (SLEEP_N), U5.14 (GPIO11)
/M2_FLAG: R15.2, U2.4 (FAULT_N), U5.5 (GPIO3)
/M2_PWM: U2.1 (EN_IN1), U5.13 (GPIO10)
/M2_SENSE: C3.1, R13.2, U5.40 (GPIO28_ADC2)
/NEOPIXEL: D3.3 (DIN), U5.6 (GPIO4)
/QSPI_SCLK: U5.52 (QSPI_SCLK), U6.6 (CLK)
/QSPI_SD0: U5.53 (QSPI_SD0), U6.5 (DI(IO0))
/QSPI_SD1: U5.55 (QSPI_SD1), U6.2 (DO(IO1))
/QSPI_SD2: U5.54 (QSPI_SD2), U6.3 (IO2)
/QSPI_SD3: U5.51 (QSPI_SD3), U6.7 (IO3)
/QSPI_SS: R2.1, R3.2, U5.56 (QSPI_SS), U6.1 (~CS)
/RUN: R7.2, SW1.2, U5.26 (RUN)
/RX: J6.2, J7.2, U5.3 (GPIO1)
/TX: U5.2 (GPIO0), U7.2
/TX_BUFFERED: J6.1, J7.1, R8.2, U7.4
/TX_CTRL: U5.4 (GPIO2), U7.1
/USB_D+: J14.3 (D+), R5.1
/USB_D-: J14.2 (D-), R6.1
/VREF: R10.2, R11.1, U1.5 (VREF), U2.5 (VREF)
/XIN: C21.1, U5.20 (XIN), Y1.3
/XOUT: R4.1, U5.21 (XOUT)
/~USB_BOOT: J13.1, R2.2
GND: C1.2, C2.1, C3.2, C4.1, C5.2, C6.2, C9.2, C10.2, C11.2, C12.2, C13.2, C14.2, C15.2, C16.2, C17.2, C18.2, C19.2, C20.2, C21.2, C22.1, D3.2 (VSS), D6.1 (A1), J3.1, J4.3, J5.3, J6.4, J7.4, J8.4, J9.4, J12.1, J14.5 (GND), J14.6 (Shield), JP3.1 (A), JP4.1 (A), R1.1, R11.2, R12.2, R14.2, R17.2, SW1.1, U1.7 (IMODE), U1.9 (PGND), U1.15 (GND), U1.16 (PMODE), U1.17 (PAD), U2.7 (IMODE), U2.9 (PGND), U2.15 (GND), U2.16 (PMODE), U2.17 (PAD), U3.4 (GND), U5.19 (TESTEN), U5.57 (GND), U6.4 (GND), U7.3 (GND), Y1.2, Y1.4
unnamed: C20.1, R4.2, Y1.1
unnamed: D1.1 (K), R1.2
unnamed: D5.2 (A), Q1.4 (G), R12.1
unnamed: J6.3, JP2.1 (A)
unnamed: J7.3, JP1.1 (A)
unnamed: C24.2, U1.13 (CPH)
unnamed: C24.1, U1.14 (CPL)
unnamed: R14.1, R16.1, U1.6 (IPROPI)
unnamed: C25.2, U1.12 (VCP)
unnamed: C26.2, U2.13 (CPH)
unnamed: C26.1, U2.14 (CPL)
unnamed: R13.1, R17.1, U2.6 (IPROPI)
unnamed: C7.2, U2.12 (VCP)
unnamed: C8.1, U3.6 (BST)
unnamed: C8.2, L1.1, U3.5 (SW)
unnamed: R6.2, U5.46 (USB_DM)
unnamed: R5.2, U5.47 (USB_DP)
VBUS: D6.2 (A2), J3.2, J12.2, Q1.5 (D), Q1.6 (D), Q1.7 (D), Q1.8 (D)
VCC: C1.1, C4.2, C7.1, C25.1, D5.1 (K), Q1.1 (S), Q1.2 (S), Q1.3 (S), U1.11 (VM), U2.11 (VM), U3.2 (EN), U3.3 (IN)

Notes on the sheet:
Make sure C5 is close to pin 45 of RP2040
Motor drivers
Crystal
C1, C4 must be rated for 35V or more
Neopixels
Make sure R5 and R6 are close to RP2040
Power
Make sure C6 is close to pin 44 of RP2040
Flash
UART connector

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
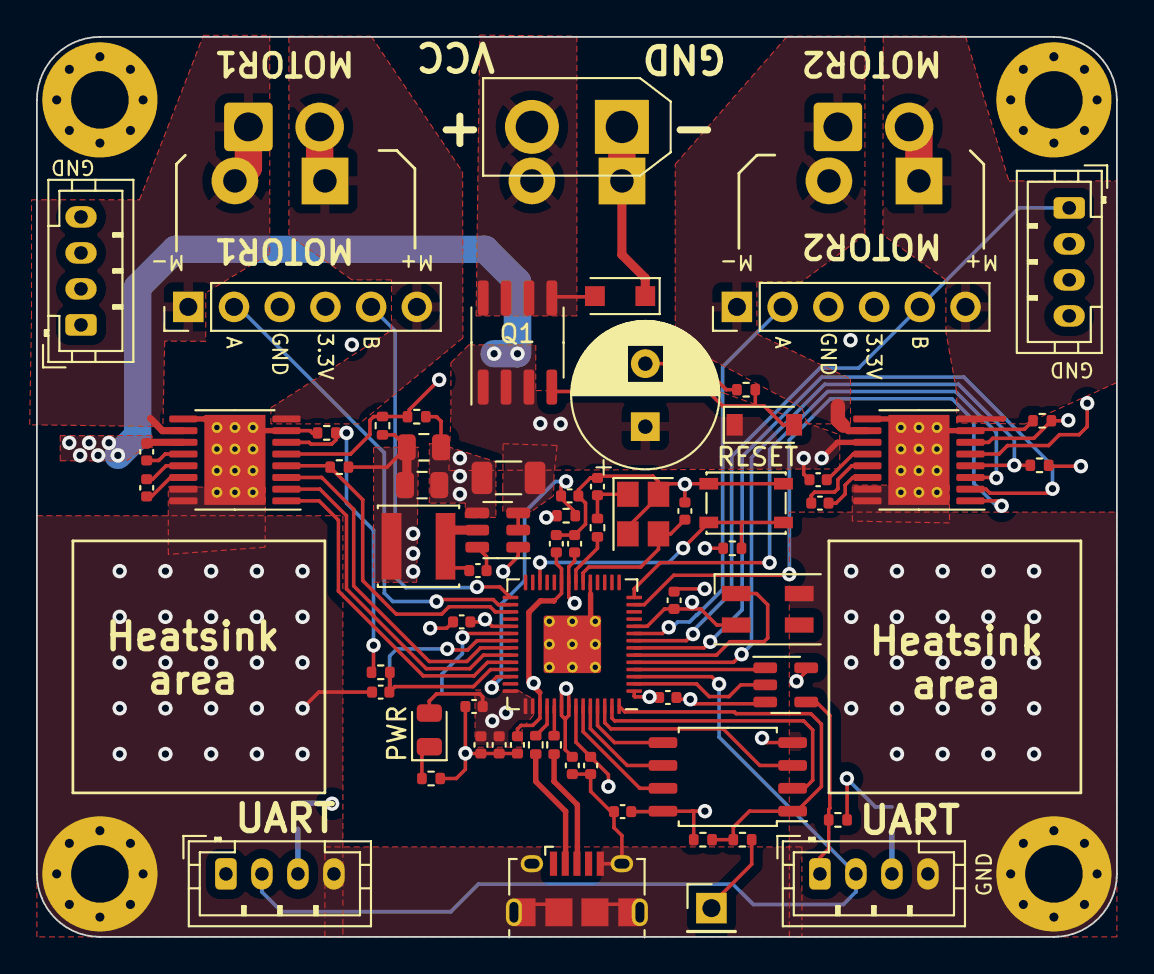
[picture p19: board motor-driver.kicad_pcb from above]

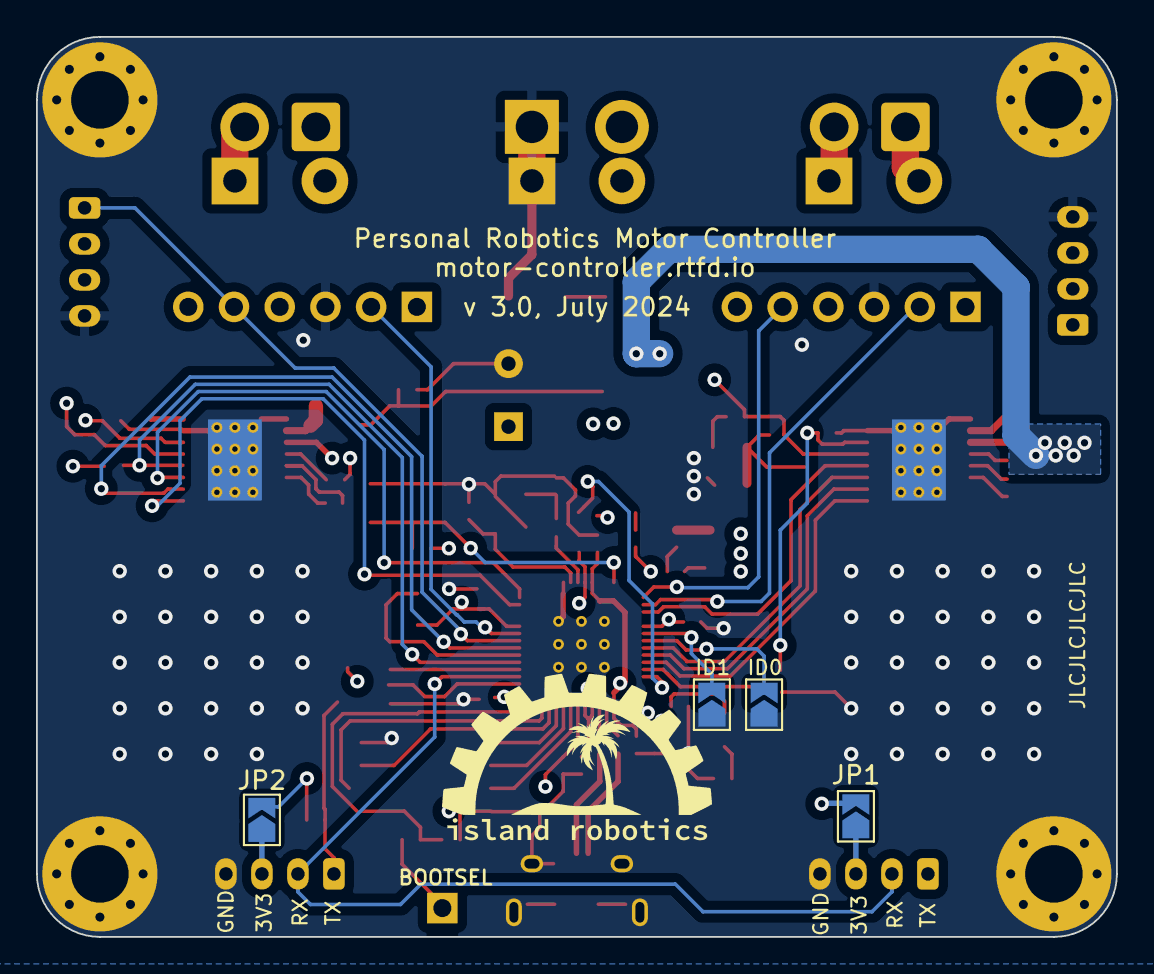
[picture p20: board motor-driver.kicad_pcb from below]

Board: 4 copper layers, 60.0 x 50.0 mm, 74 parts (4 on the bottom side), 60 nets.

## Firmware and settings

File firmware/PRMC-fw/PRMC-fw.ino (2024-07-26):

//registers
#include "pins.h"
#include "globals.h"
#include "Dynamixel.h"
//code for motors and encoders
#include "motors.h"
#include "neopixel.h"


//uncomment to allow debugging print to Serial.
//#define DEBUG_PRINT

#define SPEED_UPDATE_INTERVAL 40000 //how frequently should speed be computed? in microseconds
                                    //40 ms give frequency of 25 Hz
uint32_t last_speed_update  = micros();
uint32_t current; //in milliamps
DxlPacket instrPacket;
DxlDevice dynamixel;

void setup(){
  pins_init();    //set up pin directions
  globals_init(); // initialize global variables and register bank
  // start Serial1
  Serial1.setRX(PIN_PRMC_RX);
  Serial1.setTX(PIN_PRMC_TX);
  Serial1.begin(BAUDRATE);
  neopixel_init();
  neopixel_set_color(0);
  delay(100);
  motors_init(); //set up motor controller, etc.
  //set ID
  uint8_t id0 = 1- digitalRead(PIN_ADDR0);
  uint8_t id1 = 1- digitalRead(PIN_ADDR1);
  REGBANK[REG_MOTOR_ID] = 1 + id0 + (id1<<1);
  //initialize dynamixel interface 
  dynamixel.begin(&Serial1, BAUDRATE, REGBANK[REG_MOTOR_ID], PIN_TX_CTRL);
  //test only 
  motors_set_raw(500,500);  
  
}

void processPacket(DxlPacket * packet){
  //deal with received packet 
  uint8_t i,addr, num_bytes;
  switch (packet->instr){
    case(DXL_READ_DATA):
      addr = packet->params[0];
      num_bytes = packet->params[1]; //number of bytes to read
      if ((addr+num_bytes)<= REG_SIZE32 * 4 ) {
        dynamixel.sendPacket(num_bytes+2, NO_ERROR, &REGBANK[addr]);//FIXME: NO_ERROR
      }
      break;
    case (DXL_WRITE_DATA):
      addr = packet->params[0];
      num_bytes = packet->length - 3; //number of bytes to write
      if (addr + num_bytes <= RW_REGISTERS) {
        for (i = 0; i < num_bytes; i++) {
          REGBANK[addr+i] = packet->params[i+1];
        }
      } 
      //now, let us trigger some chnages if needed
      if (addr == REG_ENABLE){
        //turn motors on and off as needed
        motors_on_off(REGBANK[REG_ENABLE]);
      }           
      //in all cases, we set motors speed anew, and possibly (re)start the PID controllers
      motors_set_speeds();
      break;  
  }
}

void loop(){
  // check for received serial packets
  dynamixel.receivePacket(&instrPacket);
  if (instrPacket.error != RECEIVE_ERROR){
    // we have successfully received a packet, addressed to us
    processPacket(&instrPacket);
  }  
  //now, let us check if it is time to compute motor speeds and apply PID corrections
  if (micros()-last_speed_update > SPEED_UPDATE_INTERVAL) {
    last_speed_update = micros();
    //Serial.println(last_speed_update);
    compute_speed();
    if (REGBANK[REG_PID_MODE] == MODE_PID) {
        motors_pid_update();
    }
    //also, let us update motor status 
    REGBANK[REG_STATUS] = ( (1-digitalRead(PIN_ERROR2))<<1) |(1 -  digitalRead(PIN_ERROR1));
    neopixel_update();
    //and let us update current reading 
    // max value of ADC (4095) = 3.3v drop on R_prop = (3.3/1500 = 0.0022A = 2200 uA) current through R_prop
    // =  (2200/450 = 4.889) A current through H-bridge 
    current = (4889 * analogRead(PIN_M1_SENSE))/4095 ;
    Serial.print(analogRead(PIN_M1_SENSE));
    reg_save16(REG_CURRENT1, current);
    Serial.print("M1 current (mA): "); Serial.println(current);
    //same for motor2 
    current = (4889 * analogRead(PIN_M2_SENSE))/4095 ;
    //current = analogRead(PIN_M2_SENSE);
    reg_save16(REG_CURRENT2, current);
    Serial.print("M2 current (mA): "); Serial.println(current);
  }

}

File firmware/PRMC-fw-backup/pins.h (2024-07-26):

#ifndef _PRMC_PINS_H
#define _PRMC_PINS_H


//pins
#define PIN_PRMC_TX     0
#define PIN_PRMC_RX     1
#define PIN_MOTOR1_DIR   25
#define PIN_MOTOR1_PWM   26
#define PIN_MOTOR2_DIR   5
#define PIN_MOTOR2_PWM   10
#define PIN_ADDR0        23
#define PIN_ADDR1        22
#define PIN_ENC1_A       19
#define PIN_ENC1_B       18
#define PIN_ENC2_A       7
#define PIN_ENC2_B       6
#define PIN_NEOPIXEL     4
#define PIN_ERROR1       20
#define PIN_ERROR2       3
#define PIN_ENABLE1      24
#define PIN_ENABLE2      11

//function declaration to initialize pins
void pins_init();
#endif

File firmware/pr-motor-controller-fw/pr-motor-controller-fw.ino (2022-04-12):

//#include "wiring_private.h"
//registers
#include "pins.h"
#include "globals.h"
#include "i2c.h"
//code for motors, encoders, and servos
#include "motors.h"
#include "neopixel.h"


//uncomment to allow debugging print to Serial.
#define DEBUG_PRINT

#define SPEED_UPDATE_INTERVAL 40000 //how frequently should speed be computed? in microseconds
                                    //40 ms give frequency of 25 Hz
uint32_t last_speed_update  = micros();



void setup(){
    pins_init();    //set up pin directions
    globals_init(); // initialize global variables and register bank
    i2c_begin();    //start i2c bus on Wire, as a slave
    neopixel_init();
    neopixel_set_colors(BLUE,BLUE);
    motors_init(); //set up motor controller, etc. Initially it shoudl be in disabled state, with pid mode PID_OFF

    //initRegmap();
    //Serial.println("Setup ends");
}

void loop(){
    //first, check if one of motor drivers has error condition
    uint8_t new_status = (digitalRead(PIN_ERROR2)<<1) | digitalRead(PIN_ERROR1);
    //Serial.println(new_status);
    if (new_status != *motor_status){
        //update status and neopixel
        * motor_status = new_status;
        neopixel_update();
    }
    //now, check if we got enable/disable commands
    if (flag_enable) {
        //we got command from host to enable or disable motors
        flag_enable = false; //unset flag
        motors_on_off( * motor_enable);
    }

    //finally, check if we had a new speed setting for motors
    if (flag_motor_power) {
        flag_motor_power = false;
        motors_set_speeds();
    }
    //now, let su check if it is time to compute motor speeds and apply PID corrections
    if (micros()-last_speed_update > SPEED_UPDATE_INTERVAL) {
        last_speed_update = micros();
        //Serial.println(last_speed_update);
        compute_speed();
        if (*pid_mode == MODE_PID) {
            motors_pid_update();
        }
    }

}

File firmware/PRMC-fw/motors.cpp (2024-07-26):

#include <Arduino.h>
#include "globals.h"
#include "pins.h"
#include "motors.h"
#include "neopixel.h"
#include "QuadratureDecoder.h"
#include "pid.h"

int32_t prev_encoder[]={0,0};
uint32_t prev_encoder_update=micros(); //time of last update to revious encoder readign, in microseconds
int32_t enc1_index, enc2_index;

PIDcontroller SpeedController1, SpeedController2;



QuadratureDecoder decoder;

void motors_init(){
    analogWriteFreq(MOTOR_FREQ);
    analogWriteRange(MAX_MOTOR_POWER);
    prev_encoder[0]=0;
    prev_encoder[1]=0;
    speed[0]=0;
    speed[1]=0;
    SpeedController1.reset();
    SpeedController2.reset();
    //enable drivers
    digitalWrite(PIN_ENABLE1, HIGH);
    digitalWrite(PIN_ENABLE2, HIGH);
    REGBANK[REG_ENABLE] = ENABLE_M1 + ENABLE_M2;
    REGBANK[REG_PID_MODE] = MODE_NOPID;
    neopixel_update();
    //now, initialize encoders
    decoder.init(pio0);
    enc1_index = decoder.addQuadratureEncoder(PIN_ENC1_B, &encoder_raw[0]);
    enc2_index = decoder.addQuadratureEncoder(PIN_ENC2_B, &encoder_raw[1]);
}
void motors_on_off(uint8_t status){
  bool m1_status = status & 0x01;
  bool m2_status = status & 0x02;

  if (m1_status){
    //enabling motor1
    digitalWrite(PIN_ENABLE1, HIGH);
    reg_save16(REG_POWER1, 0);
  } else {
    //disabling motor1
    digitalWrite(PIN_ENABLE1, LOW);
  }
  if (m2_status){
    //enabling motor2
    digitalWrite(PIN_ENABLE2, HIGH);
    reg_save16(REG_POWER2, 0);
  } else {
    //disabling motor2
    digitalWrite(PIN_ENABLE2, LOW);
  }
}
void motors_set_speeds(){
  int16_t power1, power2;
  power1 = reg_read16(REG_POWER1);
  power2 = reg_read16(REG_POWER2);

  switch (REGBANK[REG_PID_MODE]){
    case MODE_NOPID:
      //nothing to do 
      break;
    case MODE_PID:
      //set up the PID controllers for left and right motor
      //each of them will take  as input speed (in ticks/s) and outputs a value between -1..1 - it will be later multiplied by MAX_MOTOR_POWER
      float Kp= reg_read16(REG_PID_KP)*0.0000001; //10^7
      float Ti=reg_read16(REG_PID_TI)*0.001; //time constant for integral term
      float Td=reg_read16(REG_PID_TD)*0.001; //time constant for derivative term
      float Ilim = reg_read16(REG_PID_ILIM); //integral limit, in ticks
      uint16_t motor_maxspeed = reg_read16(REG_MAX_SPEED);
      SpeedController1.configure(Kp,Kp/Ti,Kp*Td,Ilim); //Ki=Kp/Ti, Kd=Kp*Td
      SpeedController1.setTarget( (float)power1 * motor_maxspeed /MAX_MOTOR_POWER); //converting the value on-500...500 scale to ticks/s
      SpeedController2.configure(Kp,Kp/Ti,Kp*Td,Ilim);
      SpeedController2.setTarget( (float)power2 * motor_maxspeed/MAX_MOTOR_POWER); //converting the value on-500...500 scale to ticks/s
      //set initial power, as 0th approximation
      break;
  }
  motors_set_raw(power1, power2);
}
void motors_set_raw(int16_t power1, int16_t power2){
  uint8_t dir1=(power1>=0);
  uint8_t dir2=(power2>=0);
  if (power1<0) power1=-power1;
  if (power2<0) power2=-power2;
  digitalWrite(PIN_MOTOR1_DIR, dir1);
  analogWrite(PIN_MOTOR1_PWM, power1);
  digitalWrite(PIN_MOTOR2_DIR, dir2);
  analogWrite(PIN_MOTOR2_PWM, power2);
}
void compute_speed(){
  uint32_t delta=micros()- prev_encoder_update;
  update_encoders();
  int32_t count0=encoder[0];
  int32_t count1=encoder[1];
  speed[0] = ((count0-prev_encoder[0])*1000000.0)/delta; //FIXME
  speed[1] = ((count1-prev_encoder[1])*1000000.0)/delta;
  //save to register
  reg_save16(REG_SPEED1, speed[0]);
  reg_save16(REG_SPEED2, speed[1]);  
  //Serial.println(speed[0]);
  prev_encoder[0]=count0;
  prev_encoder[1]=count1;
  prev_encoder_update=micros();
}
void motors_pid_update(){
    if (REGBANK[REG_PID_MODE] == MODE_NOPID) return;
    int16_t power1 = reg_read16(REG_POWER1) + (int16_t) (MAX_MOTOR_POWER*SpeedController1.update((float)speed[0]));
    int16_t power2 = reg_read16(REG_POWER2) + (int16_t) (MAX_MOTOR_POWER*SpeedController2.update((float)speed[1]));
    //Serial.print(speed[0]);Serial.print("     "); Serial.println(powerL);
    if (power1>MAX_MOTOR_POWER) power1=MAX_MOTOR_POWER;
    else if (power1<-MAX_MOTOR_POWER) power1=-MAX_MOTOR_POWER;

    if (power2>MAX_MOTOR_POWER) power2=MAX_MOTOR_POWER;
    else if (power2<-MAX_MOTOR_POWER) power2=-MAX_MOTOR_POWER;

    motors_set_raw(power1, power2);
}

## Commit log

2021-12-11 initial upload
    [motor-driver-B_Cu.gbr, motor-driver-B_Mask.gbr, motor-driver-B_Paste.gbr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]
2021-12-13 firmware updates
    [registers.xlsx]
2021-12-14 fw update - basic functionality complete
    [BOM.xlsx, pins.xlsx]
2021-12-21 now with encoder support
    [registers.xlsx]
2021-12-25 fixing i2c issues; changed frequency
    [globals.cpp, globals.h, i2c.cpp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]
2021-12-25 started user docs
    [motor-driver.kicad_pcb]
2021-12-27 fixing register map, so I don't write int32 into 2 bytes
    [registers.xlsx]
2021-12-28 added PID mode
    [registers.xlsx]
2021-12-28 fixing firmware version number init
    [globals.cpp, motor_driver.py]
2021-12-31 added schematics
    [motor-driver.kicad_sch]
2022-01-02 updated board design files for KiCad 6.0
    [motor-driver.kicad_sch, pins.xlsx]
2022-02-15 Initial commit for version 2
    [BOM.xlsx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]
2022-02-16 docs update
    [registers.xlsx]
2022-04-14 Renaming to PRMC. Fixing enable in firmware
    [registers.xlsx]
2022-04-21 changing motor range to -1.0...1.0
2022-04-22 change current limit to 4.5A
2024-07-02 starting work on v3
    [motor-driver-CuBottom.gbr, motor-driver-CuIn1.gbr, motor-driver-CuIn2.gbr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]
2024-07-02 version 3.0.0-beta1
    [motor-driver-CuBottom.gbr, motor-driver-CuIn1.gbr, motor-driver-CuIn2.gbr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]
2024-07-26 July update
    [motor-driver-CuBottom.gbr, motor-driver-CuIn1.gbr, motor-driver-CuIn2.gbr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]
